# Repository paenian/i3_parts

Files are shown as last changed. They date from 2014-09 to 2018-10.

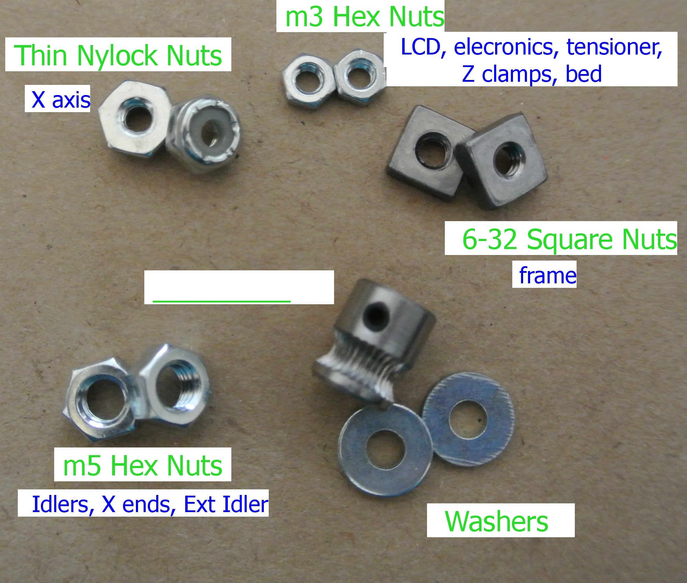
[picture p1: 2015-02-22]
bg6_pics/3D_PrinterBuild_6_Photos/labeled_parts/DSC_6048_Parts_NutsWashersAnd__.JPG

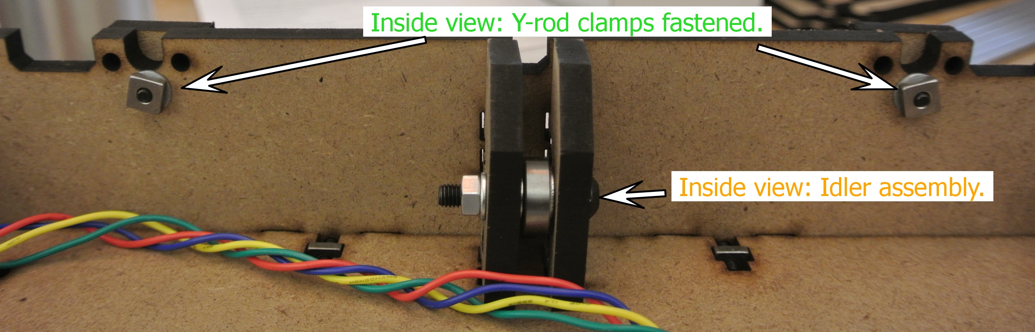
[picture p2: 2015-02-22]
bg6_pics/3D_PrinterBuild_6_Photos/DSC_6006-Y-rodClamps_InsideView_Annotated.JPG

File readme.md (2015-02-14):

A collection of parts that I use for my Graber i3 printers.  Original lasercut by Shane Graber is here: https://github.com/sgraber/Graber, and the source from Josef Prusa is here: https://github.com/josefprusa/Prusa3
<br><br>
Now featuring dual-strusion, including some parts I am using to convert my old Prusa v2 into a dual-extruder bowden machine.
<br><br>
<h4>Bill of Materails uploaded!</h4>
The full BOM is up: <pre>Paul's Prusa i3 kit - BOM.pdf</pre>
It includes everything I could think of.
<br><br>
Build Manual: <a href="https://github.com/paenian/i3_parts/wiki">https://github.com/paenian/i3_parts/wiki</a>
<br><br>
<h5>Tools</h5>
<ul>
<li>Metric Ball-end hex keys</li>
<li>Crescent Wrench</li>
<li>Soldering iron</li>
<li>Knife/scissors/wire strippers</li>
<li>Small Flathead screwdriver</li>
<li>Tweezers - preferably offset</li>
<li>Phillips screwdriver</li>
<li>Flush cutters (recommended)</li>
<li>Multimeter (recommended)</li>
</ul>
<br><br>
<h5>Major changes</h5>
<ul>
<li>Moved the LCD for better cable management</li>
<li>Added full-length top brace for increased rigidity</li>
<li>Added power-supply mounting holes</li>
<li>Added mounting holes for Rumba electronics</li>
<li>Modified bed to acommodate Y endstop rod mount</li>
</ul>

<br>
<h5>Lasercut Settings</h5>
<pre>
color - - - speed - - - power - - - corner power
Red - - - - 100 - - - -30 - - - - - 25
Green - - - 25 - - - - 30 - - - - - 25
Black - - - 12 - - - - 75 - - - - - 50
Blue - - - -12 - - - - 75 - - - - - 50
Magenta - - 12 - - - - 75 - - - - - 50
Teal - - - -12 - - - - 75 - - - - - 50
Yellow - - -12 - - - - 75 - - - - - 50
</pre>
<br>
Paul

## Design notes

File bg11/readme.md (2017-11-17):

Instructions for the BG11 build!

Firmware is copied from BG10 - will be updated later.  Nothing changing, just getting and testing the latest version of Marlin.

https://docs.google.com/presentation/d/1fhejMTiTbkoYrdEgeP_gHyqBJfEgC6iy6alJ2PzHSnQ/edit?usp=sharing

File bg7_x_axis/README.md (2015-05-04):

# This is Prusa iteration 3
Published under GPL v3
Developed primarily by Josef Prusa.

This is a new X-axis for the Build Group printers - primarily designed to eliminate parts, and make the build easier.

Also will include Y axis parts, namely a belt mount and a belt tensioner.

Paul

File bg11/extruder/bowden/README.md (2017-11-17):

The plan for Bowden is to simply re-use the extruder by adding a Bowden groovemount converter: https://www.filastruder.com/collections/e3d-spare-parts-and-accessories/products/bowden-couplings-all-types

So all you need is the clamp for mounting the hotend.

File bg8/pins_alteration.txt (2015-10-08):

Copy the pins_arduino.h file into this directory:
/home/paenian/reprap/arduino-1.6.5/hardware/arduino/avr/variants/mega

Better yet, we should copy the mega directory and create a new board variant - maybe look up how to do that?

Paul

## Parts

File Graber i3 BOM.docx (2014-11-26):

you will need additional parts to finish:

PART | QTT | | PART | QTT
6-32 x 3/4" | 41 | | Threaded rod
6-32 x 0.5" | 6 | | 5/16" x 2" (x & y-belt idler) | 2
6-32 x 1' | 2
6-32 x 1,1/4" (X-Car) | | | 5mm x 11.5" (Z-Axis) Alt - 10-24 x 11.5" | 2
6-32 x 1,3/4" | 4
Nut 6-32 Nylon Insert | 8
Nut 5/16" | 61 | | Smooth Rod
Nut M5 (.8mm / thread) Alt - 10-24 (.945mm / thread) | 2 | | http://www.use-enco.com/CGI/INSRIT?PMAKA=505-0240&PMPXNO=942271&PARTPG=INLMK32
Washers 6-32 | 2 | | 8mm x 13.5" (Y-Axis) | 2
Washers 5/16" | 6 | | 8mm x 12.5" (Z-Axis) | 2
M3 x 10mm (for step motors) | 2 | | 8mm x 15 3/4" (X-Axis) | 2
M3 x 25mm (RAMPS mount) | 15
M3 x 20-25 mm (Heated Bed) | 3 | -4 | Nema 17 Step motor | 5
M3 Nut Nylon Insert | 3-4 | | Micro Switch (end stops) | 3
Spring (heated bed mount) | 3-4 | | Electronics Board (RAMPS or other) | 1
Zip Tie 4" | 7
| | | Extruder (w/ 3 more 608zz bearings) | 1
608zz (for Y and X idler)
PVC Tubing 20mm (Z-Axis) | 2 | | LM8UU | 10
| 2

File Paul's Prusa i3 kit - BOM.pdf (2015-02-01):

Part | Size | Length/type | Quantity | description | Source | parts*bots | single part cost | total
Screws | 6-32 | 1/2" | 7 | Y motor mount, 3 hotend mount, 2 power supply mount | mcmaster | 7 | $0.12 | $0.85
| | 3/4" | 50 | frame | mcmaster | 50 | $0.20 | $9.80
| | 1 1/4" | 7 | 6 X carriage, 1 extruder clamp | mcmaster | 7 | $0.30 | $2.11
| | 1 3/4" | 8 | X ends | mcmaster | 8 | $0.62 | $4.95
| m3 | 10mm | 30 | 4 X, 3 Y, 8 ZZ, 3 E, 8 z clamp, 4 endstops | mcmaster | 30 | $0.07 | $2.06
| m3 | 20mm | 15 | 4 LCD, 4 electronics, 4 heatbed mount, 1 extruder tensioner, 2 endstops | mcmaster | 15 | $0.09 | $1.28
| m4 | 18mm | 3 | Power supply mount | mcmaster | 3 | $0.11 | $0.33
| m5 | 30mm | 6 | 2 X and Y Idler, 4 spool rollers | mcmaster | 6 | $0.12 | $0.74
| m5 | 14mm | 1 | extruder idler | mcmaster | 1 | $0.12 | $0.12
| All screws are button-head except the m4
Nuts | 6-32 | square | 58 | | mcmaster | 58 | $0.02 | $0.95
| 6-32 | thin nylock | 14 | | mcmaster | 14 | $0.03 | $0.37
| m5 | hex | 9 | 2 for x ends, 2 for idler screws, 1 extruder idler, 4 spool rollers | mcmaster | 9 | $0.02 | $0.19
| m3 | hex | 27 | 4 LCD, 4 electronics, 4 heatbed, 1 idler, 8 z clamp, 6 endstop | mcmaster | 27 | $0.01 | $0.38
Washers | 6-32 | flat | 100 | frame, motors, ps, etc. This washer will fit m3, m4 and 6-32 screws just fine. | mcmaster | 100 | $0.01 | $1.35
| m5 | flat | 6 | idlers | mcmaster | 6 | $0.02 | $0.13
Bearings | lm8uu | linear | 10 | 3 X, 3 Y, 4 Z | aliexpress | 10 | $0.60 | $6.00
| 605zz | roller | 7 | 3 idlers, 4 spool rollers | aliexpress | 7 | $0.42 | $2.94
Smooth Rod | m8 | 400mm | 2 | X rods - 15.75" | misumi | 2 | $8.44 | $16.88
| | 342mm | 2 | Y rods - 13.5" | misumi | 2 | $8.44 | $16.88
| | 318mm | 2 | Z rods - 12.5" | misumi | 2 | $8.44 | $16.88
| m8 | 36" drill rod | 3 | | mcmaster | 3 | $5.70 | $17.10
Threaded Rod | m5 | 300mm | 2 | mcmaster | 2 | $5.12 | $10.24
Wire | 16 gauge power wire | 2 conductor | 5 | 2 2' runs PS to electronics | mcmaster powe | 5 | $0.69 | $3.45
| | | | 1 1' run electronics to heatbed | | 1 | $0.69 | $0.69
| | | | cut up a bit to install power switch | | 0 | $0.69 | $0.00
Other | motors | nema 17 | 5 | | kysan | 5 | $16.00 | $80.00
| electronics | rumba | 1 | Includes heatbed, pulleys, belts, LCD, grub screws, wiring | reprapdiscount | 1 | $159.00 | $159.00
| Power Switch | | 1 | | amazon | 1 | $6.00 | $6.00
| Power cord | computer cord | 1 | | amazon | 1 | $5.00 | $5.00
| fuse | | 1 | | amazon | 1 | $1.20 | $1.20
| female spade connectors | 22/18 | 6 | | http://www.ama (http://www.amazon.com/gp/product/B001766LZO/ref=ox_sc_act_title_1?ie=UTF8&psc=1&smid=A1PH6OFMJYJKNX) | 6 | $0.13 | $0.80
| power supply | 24v 15a | 1 | | amazon | 1 | $25.00 | $25.00
| induction sensor | 8mm range, 18 | 1 | | amazon | 1 | $8.20 | $8.20
| plastic | for me to print w | 1 | | my print cave | 1 | $20.00 | $20.00
| borosilicate glass | 8x8.5x1/8 | 1 | | cincinatti gasket | 1 | $22.00 | $22.00
| Kapton tape sheet | 8x8 | 2 | | amazon | 2 | $3.59 | $7.18
| plastic reel | for you | 1 | | Microcenter | 1 | $25.00 | $25.00
| MDF sheet | 1/4"x48x24 | 1 | Cut to 39x24 before laser cutting | home depot | 1 | $6.00 | $6.00
| Laser Cutting | in hours | 1.5 | it's a lot of cuts. | Nova Labs | 1.5 | $20.00 | $30.00
| Paul putting all this toget | brownie points | 16 | | | 16 | | $0.00
| Stanley organizer | 25 compartment | 1 | | http://www.ama (http://www.amazon.com/Stanley-25-Removable-Compartment-Professional-Organizer/dp/B00005QWYF) | 1 | $13.00 | $13.00
| hotend | e3d V6 | 1 | | filastruder | 1 | $80.00 | $80.00
| Bed Clips | 3/4" wide, 5/16" | 4 | | mcmaster | 4 | $0.07 | $0.28
| Zip Ties | 4" | 25 | | mcmaster | 25 | $0.02 | $0.55
Printed Parts | Power Supply Cover | 1 | 1 | 0
| Z clamps | 4 | 4 | 0
| Endstops | 2 | 2 | 0
| Stop Switch | 1 | 1 | 0
| Encoder Dial | 1 | 1 | 0
| Extruder Mount | 1 | 1 | 0
| Extruder Mount | 1 | 1 | 0
| Induction Mount | 1 | 1 | 0
Budget | | | $550
Totals | | pre-cut hardened steel | $588.77
| | drill rod, needs to be cut to length | $555.23
# of Printers | 1 | pre-cut leftover | -$39

| | drill rod leftover | -$5
| | Note: Shipping isn't included anywhere.

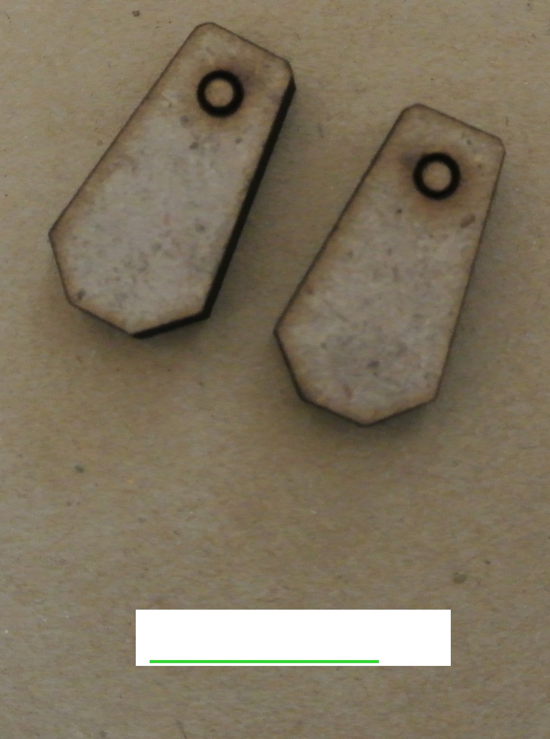
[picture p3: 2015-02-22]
bg6_pics/3D_PrinterBuild_6_Photos/labeled_parts/DSC_6039_Cropped.JPG

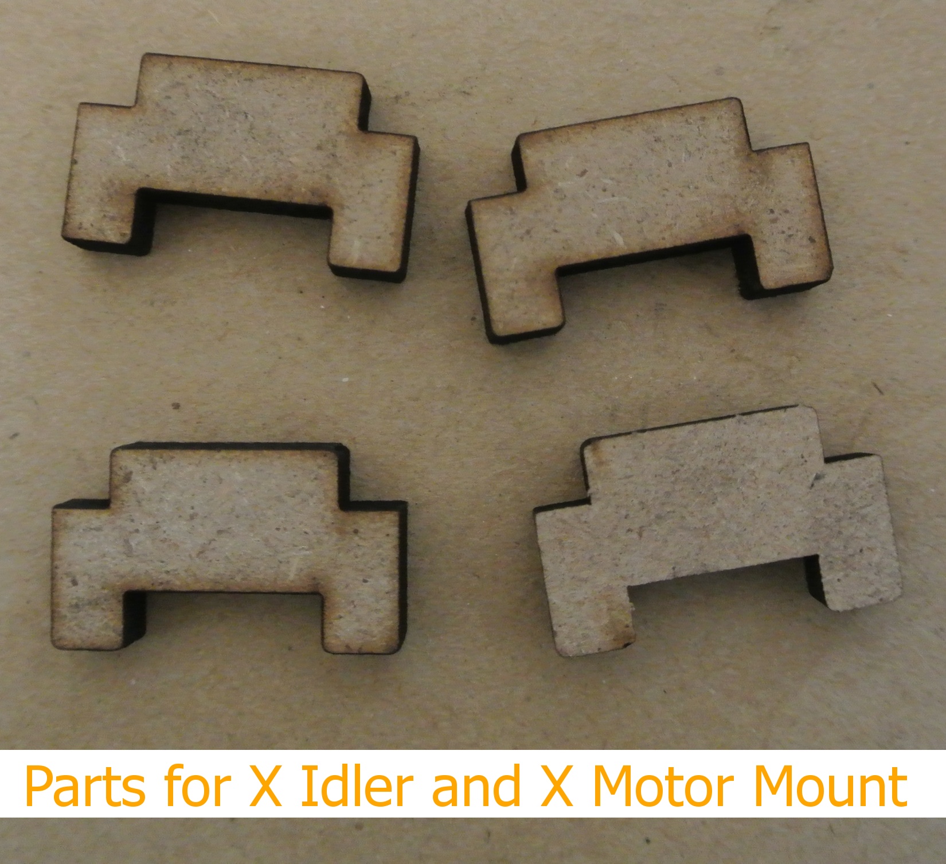
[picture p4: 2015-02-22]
bg6_pics/3D_PrinterBuild_6_Photos/labeled_parts/DSC_6040_Parts_X-IdlerAndX-MotorMount.JPG

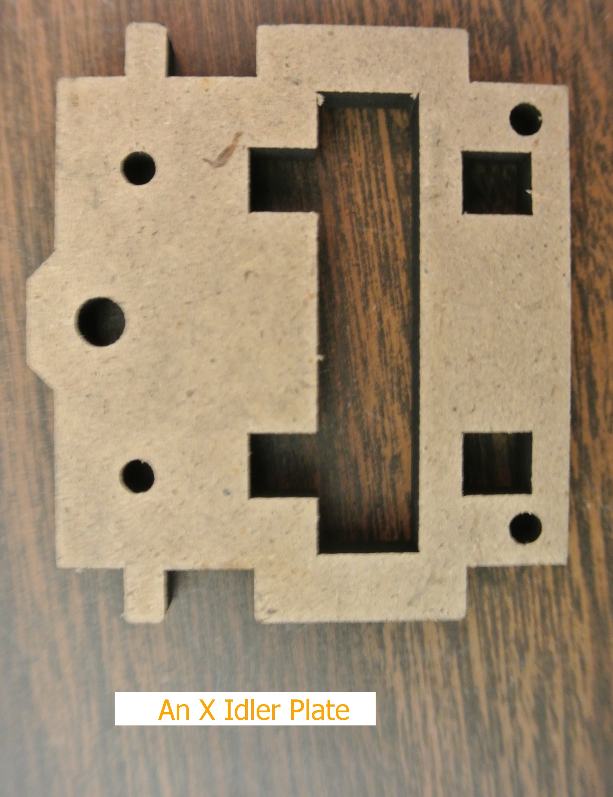
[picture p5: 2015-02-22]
bg6_pics/3D_PrinterBuild_6_Photos/labeled_parts/DSC_6013_Parts_X-IdlerPlate1.JPG

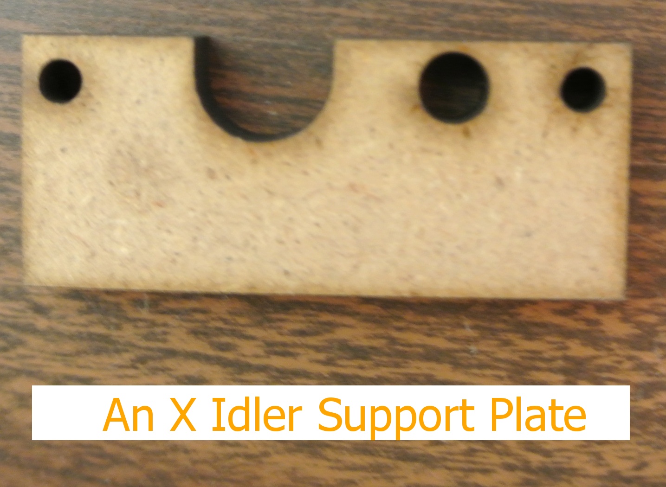
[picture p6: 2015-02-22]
bg6_pics/3D_PrinterBuild_6_Photos/labeled_parts/DSC_6021_Parts_X-IdlerSupportPlate2.JPG

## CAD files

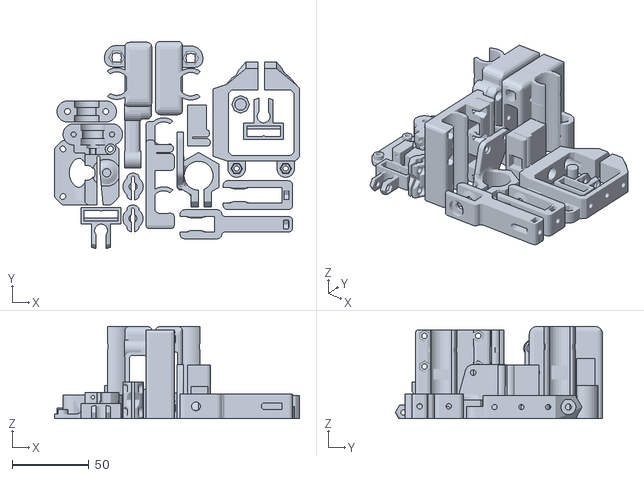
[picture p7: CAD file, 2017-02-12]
bg10/full_plate.stl
159.9 x 135.4 x 60.2

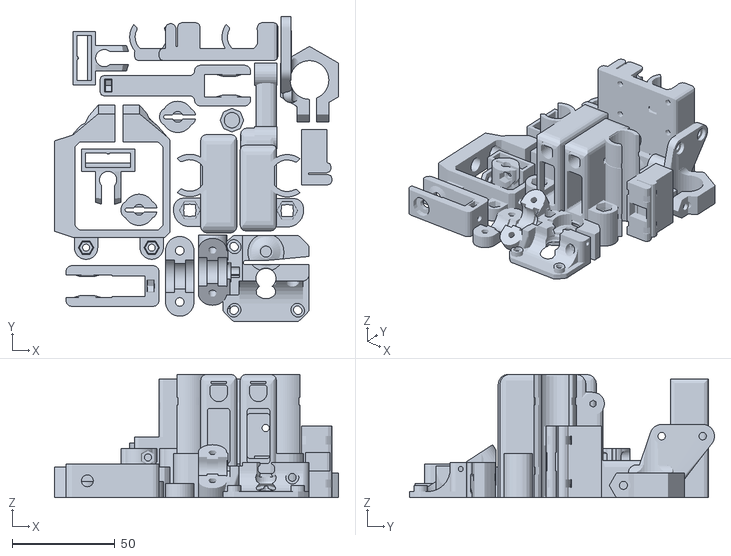
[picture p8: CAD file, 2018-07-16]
bg11/full_plate.stl
138.6 x 148.7 x 60.2

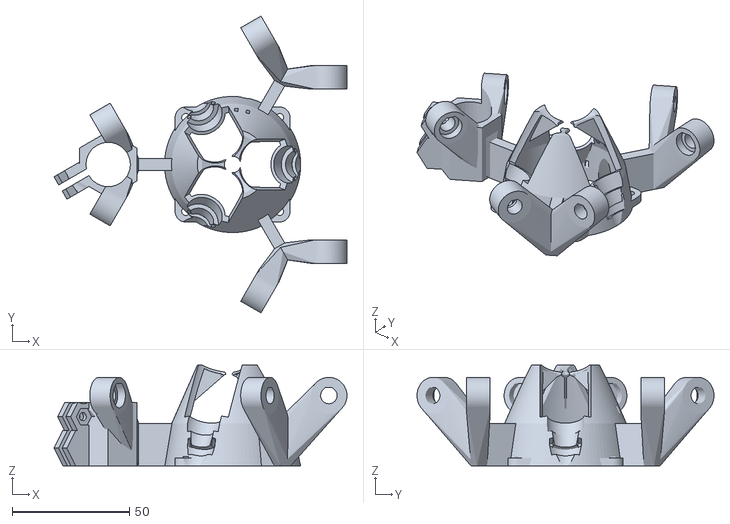
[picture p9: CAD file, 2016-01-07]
bg8/x_axis/diamond_hotend_assembly.stl
124.8 x 126.5 x 43.0

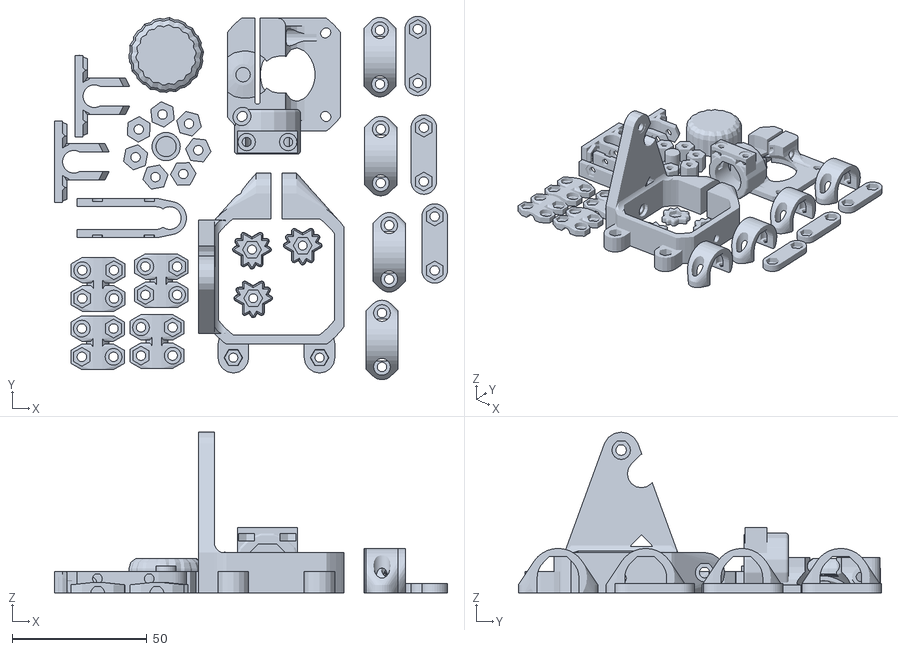
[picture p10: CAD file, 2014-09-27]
i3_full_plate.stl
145.8 x 134.8 x 59.7

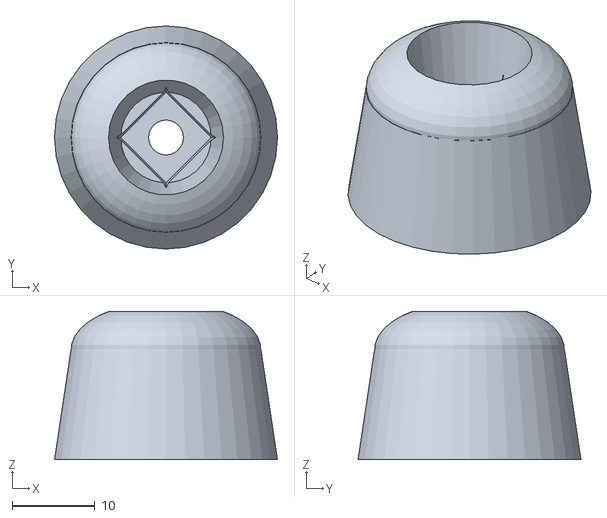
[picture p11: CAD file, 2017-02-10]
bg10/extras/foot.stl
26.9 x 26.9 x 17.9

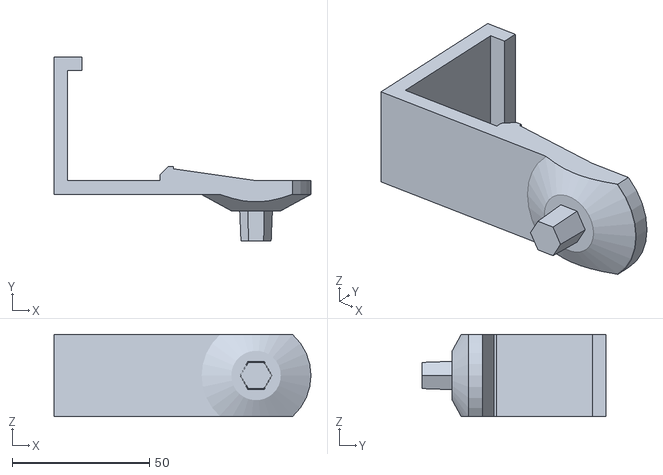
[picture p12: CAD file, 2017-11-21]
bg10/extras/spool_roller/spool_bearing_mount.stl
93.5 x 67.0 x 30.0

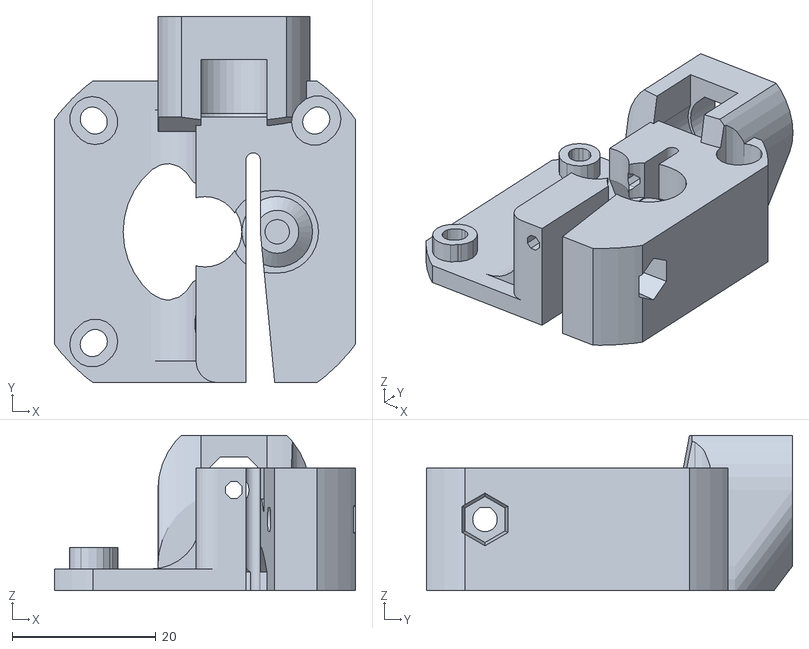
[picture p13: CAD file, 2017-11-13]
bg10/extruder/bowden/motormount_extruder_bowden.stl
42.0 x 51.0 x 21.6

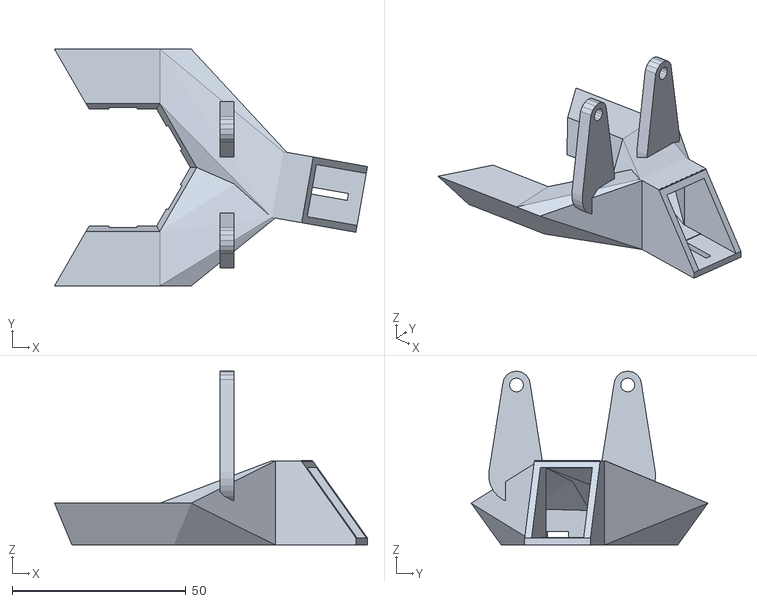
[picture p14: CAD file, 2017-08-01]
bg10/extruder/cooling_fan_mount.stl
90.0 x 68.1 x 50.0

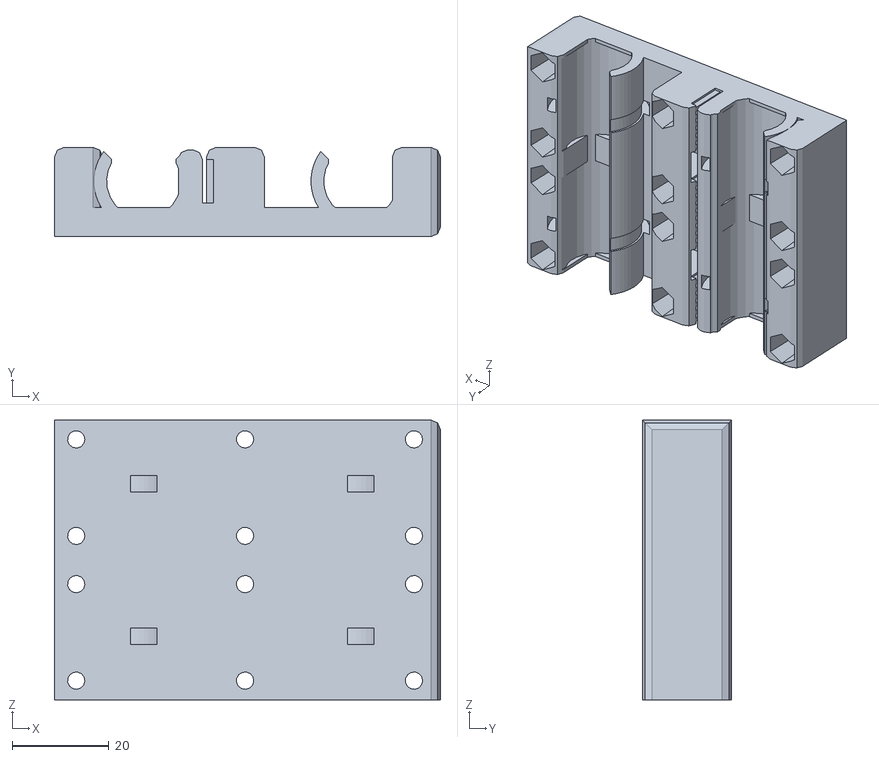
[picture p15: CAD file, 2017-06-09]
bg10/x_axis/x-carriage_aero.stl
80.0 x 18.5 x 58.0

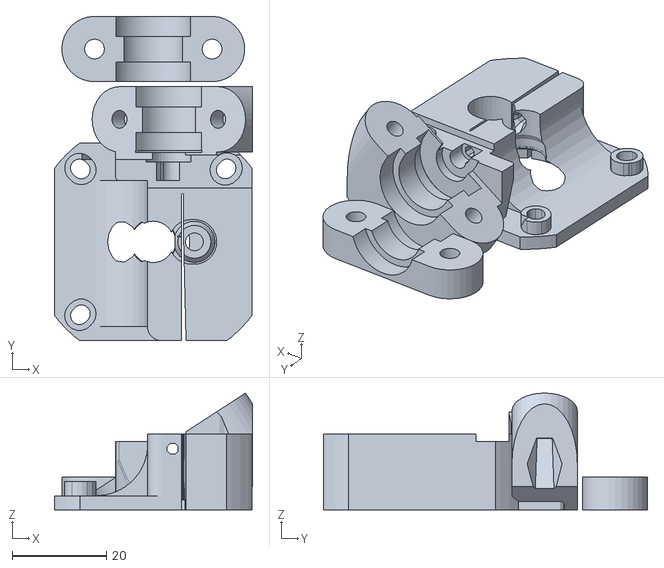
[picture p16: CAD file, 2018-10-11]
bg11/extras/bondtech/motormount_bondtech.stl
42.1 x 69.0 x 24.9

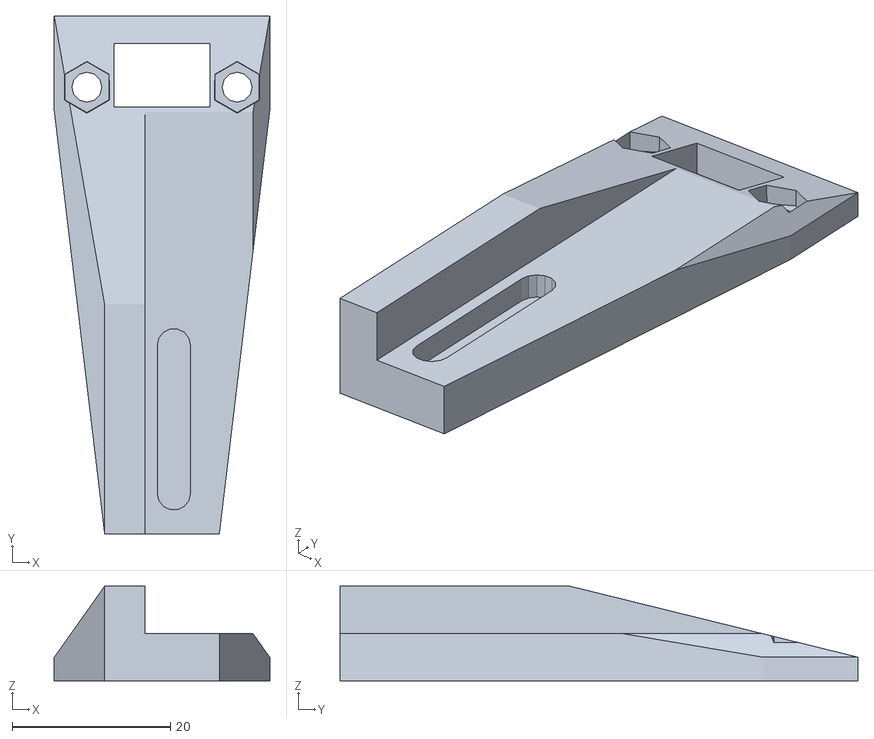
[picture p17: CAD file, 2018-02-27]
bg11/extras/diff_ir_drop_mount.stl
27.2 x 65.5 x 12.0

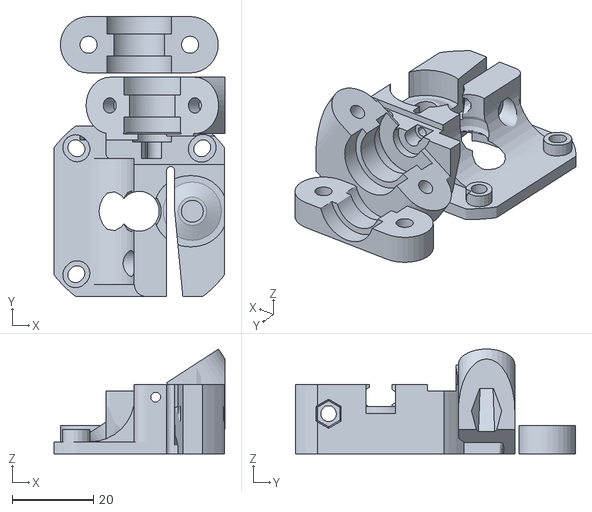
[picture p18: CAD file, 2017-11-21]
bg11/extruder/motormount_extruder_v2.stl
42.1 x 69.0 x 25.9

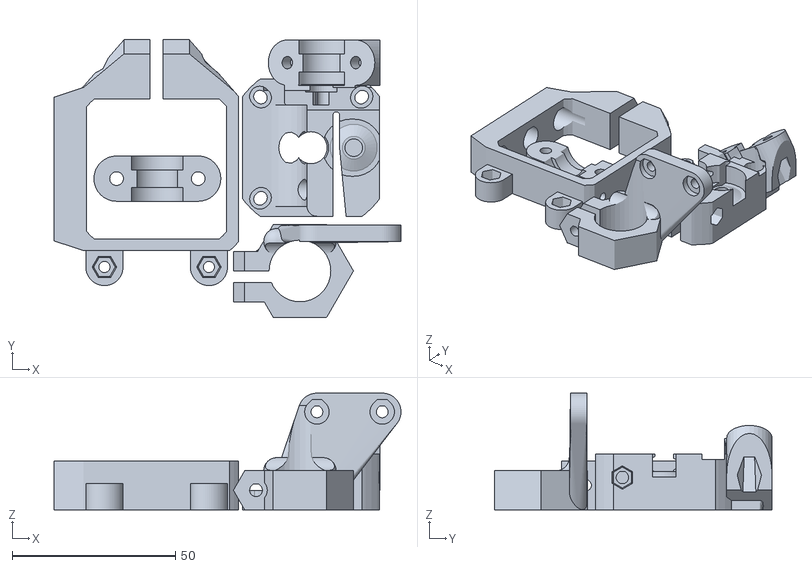
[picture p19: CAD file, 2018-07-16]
bg11/extruder_plate.stl
106.3 x 85.0 x 35.8

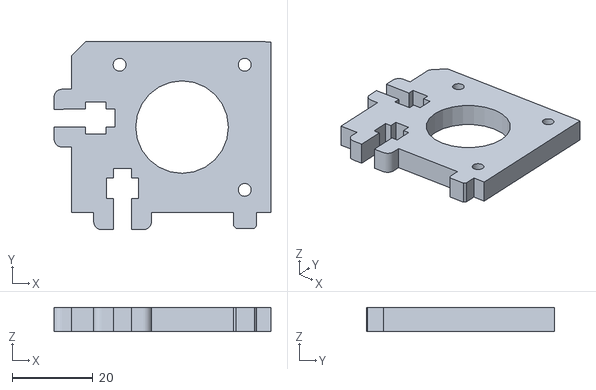
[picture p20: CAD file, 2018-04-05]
bg11/frame/y_motor_mount.stl
53.8 x 46.7 x 6.00

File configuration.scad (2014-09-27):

////////////////////////////
//  This is a Delta printer design by Paul Chase.
////////////////////////////


slop = .2;
wall = 5;



////////////////////////////
//Standard Sizes
////////////////////////////
m3_nut_rad = 6.05/2+slop;
m3_nut_height = 2.4+slop;
m3_rad = 3/2+slop;
m3_cap_rad = 3.25;
m3_washer_rad = 7/2+slop;

m4_nut_rad = 7.66/2+slop;
m4_nut_height = 3.2;
m4_rad = 4/2+slop;
m4_cap_rad = 7/2+slop;
m4_washer_rad = 2*m4_rad;

m5_nut_rad = 9.05/2+slop;
m5_nut_height = 4.7;
m5_rad = 5/2+slop;
m5_cap_rad = 8/2+slop;
m5_washer_rad = 2.1*m5_rad;
m5_cap_height = 2;

//for the tiny m3 bearings
623_width = 4;
623_rad = 10.05/2+slop;
623_bore = m3_rad;
623_inner_shoulder = 623_bore+(623_rad-m3_rad)/3;
623_outer_shoulder = 623_rad-(623_rad-m3_rad)/3;

//spacers
spacer_rad = 6/2+slop;
spacer_len = 2-slop/2;

eccentric_rad = 7.2/2+slop;
eccentric_washer_rad = 15/2+slop;
eccentric_screw_rad = 7/2+slop;
eccentric_height = 2.5;



//////////////////////////////
//Useful global functions
//////////////////////////////
module cap_cylinder(r=1, h=1, center=false){
	render() union() {
		cylinder(r=r, h=h, center=center);
		intersection(){
			rotate([0,0,22.5]) cylinder(r=r/cos(180/8), h=h, $fn=8, center=center);
			translate([0,-r/cos(180/4),0]) rotate([0,0,0]) cylinder(r=r/cos(180/4), h=h, $fn=4, center=center);
		}
	}
}

module 623_bearing(){
	union(){
		//outer
		color([.75,.75,.75]) difference(){
			cylinder(r=623_rad, h=623_width);
			translate([0,0,-.1]) cylinder(r=623_outer_shoulder, h=623_width+.2);
		}
		//middle
		color([.25,.25,.25]) difference(){
			translate([0,0,.25]) cylinder(r=623_outer_shoulder, h=623_width-.5);
			translate([0,0,-.1]) cylinder(r=623_inner_shoulder, h=623_width+.2);
		}
		//inner
		color([.75,.75,.75]) difference(){
			cylinder(r=623_inner_shoulder, h=623_width);
			translate([0,0,-.1]) cylinder(r=623_bore, h=623_width+.2);
		}
	}
}

module 623_bearing_cone(rad = 623_rad, height = 5, solid=1, nut_trap=0){
	cone_h = rad-623_inner_shoulder;
	if(nut_trap==1){
		if(solid==1){
			union(){
				echo("cone_height", cone_h);
				cylinder(r1=623_inner_shoulder, r2=rad, h=cone_h);
				translate([0,0,cone_h]) cylinder(r=rad, h=height-cone_h);
			}
		}else{
			//bore
			translate([0,0,-.1]) rotate([0,0,90]) cap_cylinder(r=623_bore, h=height+.5);
			//nut trap
			#translate([0,0,height-m3_nut_height]) hull(){
				cylinder(r1=m3_nut_rad, r2=m3_nut_rad+.5, h=m3_nut_height+.5, $fn=6);
				translate([30,0,0]) cylinder(r1=m3_nut_rad, r2=m3_nut_rad+.5, h=m3_nut_height+.5, $fn=6);
			}
		}
	}else{
		if(solid==1){
			cylinder(r1=623_inner_shoulder, r2=rad, h=height);
		}else{
			translate([0,0,-.1]) rotate([0,0,90]) cap_cylinder(r=623_bore, h=height+.5);
		}
	}
}

module 623_bearing_mount(rad = 623_rad+2, height=5, solid=1){
	if(solid==1){
		union(){
			cylinder(r=rad, h=height);
		}
	}else{
		translate([0,0,height-623_width+slop]) cap_cylinder(r=623_rad, h=623_width*2);
		//translate([0,0,height-623_width]) cap_cylinder(r=623_outer_shoulder, h=623_width*2);
		translate([0,0,-height]) cap_cylinder(r=m3_cap_rad+.25, h=height*3);
	}
}

module barbell (x1,x2,r1,r2,r3,r4)
{
	x3=triangulate (x1,x2,r1+r3,r2+r3);
	x4=triangulate (x2,x1,r2+r4,r1+r4);
	render()
		difference(){
			union(){
				translate(x1) circle (r=r1);
				translate(x2) circle(r=r2);
				polygon (points=[x1,x3,x2,x4]);
			}
		translate(x3) circle(r=r3,$fa=5);
		translate(x4) circle(r=r4,$fa=5);
	}
}

function triangulate (point1, point2, length1, length2) =
point1 + length1*rotated(
atan2(point2[1]-point1[1],point2[0]-point1[0])+
angle(distance(point1,point2),length1,length2));

function distance(point1,point2)=
sqrt((point1[0]-point2[0])*(point1[0]-point2[0])+
(point1[1]-point2[1])*(point1[1]-point2[1]));

function angle(a,b,c) = acos((a*a+b*b-c*c)/(2*a*b));

function rotated(a)=[cos(a),sin(a),0];
function rotate_vec(v,a)=[cos(a)*v[0]-sin(a)*v[1],sin(a)*v[0]+cos(a)*v[1]];

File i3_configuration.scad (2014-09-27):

////////////standard variables.  Shouldn't need to change 'em.  Except maybe slop.
motor_w = 42;
motor_r = 50/2;

m3_nut_rad = 6/cos(30)/2;
m3_nut_height = 3;
m3_rad = 1.8;
m3_cap_rad = 3.25;

m4_rad = 2+slop;
m4_nut_rad = 7.8/2+slop;
m4_nut_height = 3.2;
m4_cap_rad = 7/2+slop;

m5_nut_rad = 8.4/cos(30)/2+slop;
m5_nut_height = 4+slop;
m5_rad = 2.8;

//english sizes - 6-32 - for graber i3 clamp
632_dia = 3.5;
632_rad = 632_dia/2+slop;
632_nut_rad = 8.25/cos(45)/2;
632_cap_dia = 6.5;
632_cap_rad = 632_cap_dia/2+slop;
632_cap_height = 2+slop;
632_nut_height = 5;

$fn=32;

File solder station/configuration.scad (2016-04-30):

mdf_wall = 6.5;
mdf_tab = 15;

wall = 5;

screw_slop = .2;
slop = .2;
laser_slop = -.1;

smooth_rod_rad = 10/2+laser_slop+.1;

//these can't change - measured values.
beam = 20;
bed_screw_sep = 309;
bed = 300;

layer_height=.2;

//this is for using the big idlers
//idler_rad = 17.5/2;
//idler_flange_rad = 22/2;

//this is using flanged bearings, and no plastic
idler_rad = 10/2;
idler_flange_rad = 15/2;

pulley_rad = 13/2;
pulley_flange_rad = 18/2;

//using the mini V-wheels
wheel_rad = 11.5/2;
wheel_clearance = 18;
wheel_height = 9;
wheel_flange_rad = 16/2;

eccentric_rad = 7.3/2;
eccentric_flange_rad = 11/2;

//frame lengths - may be dependent on wall above.
frame_x = 500;  //we lose more in X because of the endcaps - it's where all the motors etc. will hide.
frame_y = 420;  //(420-300)/2-beam=40mm clearance on either side of the printer.
frame_z = 420;  //because square is nice.

foot_height = 60;       //tall foot, cuz the Z motor will be underneath.

echo("BOM: 4, reg rail, 2020", frame_x, "Frame");

//motor size and placement variables
motor_w = 42;
motor_r = 52/2;
motor_y = frame_y/2-beam-pulley_rad; //distance motors are from the center.

belt_thick = 6;
belt_width = 2;


//gantry - might want to make it bigger
echo("BOM: 1, v-rail, 2020", frame_y, "Gantry");

//bed lengths
bed_x = 300+beam*2;
bed_y = 300;  //the screwholes on the bed should line up with the long_bed rails.
echo("BOM: 2, reg rail, 2020", bed_x, "Bed mount");
echo("BOM: 3, reg rail, 2020", bed_y, "Bed mount");  //might want more than three - to hold insulation well.

//standard screw variables
m3_nut_rad = 6.01/2+slop;
m3_nut_height = 2.4;
m3_rad = 3/2+slop;
m3_cap_rad = 3.25;
m3_cap_height = 2;

m4_nut_rad = 7.66/2+slop;
m4_nut_height = 3.2;
m4_rad = 4/2+slop;
m4_cap_rad = 7/2+slop;
m4_cap_height = 2.5;

m5_nut_rad = 8.79/2;
m5_nut_rad_laser = 8.79/2-.445;
m5_nut_height = 4.7;
m5_rad = 5/2;
m5_cap_rad = 10/2+slop;
m5_cap_height = 3;


//some enums
MALE = 1;
FEMALE = -1;

//makes all the holes have lots of segments
$fs=.5;
$fa=.1;

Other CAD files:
bg9/full_plate.stl
bg11/small_bits/z_clamp.stl
bg11/x_axis/inc/splitter_coupler.stl
bg7_x_axis/anglefan.stl
bg11/x_axis/configuration.scad
1.75_bowden_tap_m5idler.stl
1.75_grooveclamp_clamp.stl
1.75_grooveclamp_m5idler.stl
1.75_groovemount_m5idler.stl
1.75_mark8_bowden_m5idler.stl
1.75_mark8_grooveclamp_m5idler.stl
End_Stop_Holder.scad
LM8UU_holder_ziptie.scad
PowerSupply.scad
PowerSupply.stl
anglefan.stl
bg10/extras/spool_roller/bearing.scad
bg10/extras/spool_roller/bearing_lifter.scad
bg10/extras/spool_roller/spool_bearing.scad
bg10/extras/spool_roller/spool_roller.scad
bg10/extras/spool_roller/spool_roller.stl
bg10/extras/spool_roller/top_spool_roller.stl
bg10/extruder/aero_flange.stl
bg10/extruder/cooling_fan_mount_rakish.stl
bg10/extruder/extruder_mount.stl
bg10/extruder/extruder_mount_aero.stl
bg10/extruder/motormount_extruder_v2.scad
bg10/extruder/motormount_extruder_v2.stl
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

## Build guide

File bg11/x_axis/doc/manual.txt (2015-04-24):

Assembly

This document will guide you through putting together your Prusa i3.
Please read it through briefly before starting your build, and make sure you have everything you need to continue.
It's frustrating to be stuck with a half-finished machine because you are missing a part or tool.
It's recommended to do the assembly with 2 or more people. If you are doing this alone, do the instructions in order.
If there are two of you, each step is marked P1 or P2. Decide which one of you is Player 1 and act accordingly.
If there are more than two of you, split into two teams.

===Assemble the extruder (P1)===
There are multiple forms of extruder. These instructions cover two common variants.

==The gregstruder==
Plastic parts needed:
-Extruder body
-Extruder idler
-Extruder large gear
-Extruder small gear
Other parts needed:
-1 NEMA17 motor
-1 hotend
-1 M3x8 grub screw
-6 M3 nuts
-3 M3x40 bolts
-1 M8x20 grub screw
-1 M8 hobbed bolt
-4 M8 washers
-2 M8 nuts
-3 608 skateboard bearings
-3 M3x10 bolts
(optional) 2 short, stiff springs or silicone pads
Tools needed
-Wrench/spanner to fit M8 (preferably 2)
-Soldering iron
-Drill with 8mm and 3mm bits
-File
-Screwdriver or allen key to fit your M3 bolt heads and the M3 grub screw

Take the extruder body and snap off the small support piece attached to it. It should separate easily. If it leaves a messy surface, clean the surface up.
Use the drill to drill through the 8mm hole in the extruder body, the 3mm holes for the motor bolts, the 2 3mm mounting holes on the bottom and the 3mm hole for the idler (where the support piece was).
Melt two M3 nuts into the nut traps over the mounting holes.
Drill through the filament channel to make sure it's clear.
Place 1 608 bearing on the M8x20 grub screw and push it into the idler. It will only fit if the bearing is on the middle of the grub screw. It will click in place.
Attach the idler to the extruder body and fix it with the M3x40 bolt. Make sure the bolt head is on the FLAT side of the extruder body. You can put a nut on the bolt if you want, but don't tighten it very tightly.
Place an M3 nut in the small gear and fix it in place with the M3x8 grub screw. Slide the gear onto the motor shaft and fix it in place with the grub screw. Do not overtighten, and make sure the motor can turn freely with the gear in place.
Attach the motor to the extruder body with the 3 M3x10 bolts. The bolt heads go on the FLAT side of the extruder body.
Place 2 608 bearings in the recesses in the extruder body. 
Place the hobbed bolt in the large gear. If it's too loose, pad it a bit until it sits tight. Place two washers on the opposite (flat) side of the gear and slide the hobbed bolt through the two bearings into the extruder body. The gear teeth will mesh with the small gear already there. If they don't, adjust the position of the motor and/or the gear on the motor shaft until they do. Make sure the bobbing on the bolt aligns with the filament channel. If necessary, add another washer between the gear and the extruder body. Place a washer followed by 2 M8 nuts on the opposite side of the extruder body to fix the bolt in place.
If you are using springs or silicone pads, place those on the remaining two M3x40 bolts. Place two nuts into the nut recesses above the two bearings. Use the M3x40 bolts to fix the idler in place. You will adjust the tension later when you insert filament, so don't worry about that for now. 
Assemble your hotend according to your specific hotend's assembly instructions. I am assuming you have a hotend that is matched to your extruder body.
Attach the hotend to the extruder. If your hotend has a flat mounting plate, make sure the holes on it align with the holes on the extruder body so that the filament channel leads into the hotend. Redrill holes as necessary if something does not fit.

==The raldrich geared stepper extruder==

Plastic parts needed:
-Extruder body
-Extruder idler
-Extruder body spacer
Other parts needed:
-1 geared stepper motor
-1 hotend
-2 M3x30 bolt
-6 M3 nuts
-1 filament drive gear
-1 M3x8 grub screw
-1 M4 x20 bolt
-1 624 bearing
-4 M3x40 bolts
-4 M3 washers
(optional) 4 short, stiff springs or silicone pads
Tools needed
-Soldering iron
-Drill with 8mm and 3mm bits
-File
-Screwdriver or allen key to fit your M3 and M4 bolt heads and the M3 grub screw

Use the drill to drill through the 3mm holes for the motor bolts, the 2 3mm mounting holes on the bottom and the 4mm hole in the idler.
Drill through the filament channel to make sure it's clear.
Place the 624 bearing in the idler and fix it with the M4x20 bolt.
Place the spacer on the motor and make sure it aligns correctly with the extruder body.
Attach the drive gear to the motor shaft with the grub screw. Adjust the position of the drive gear to align with the filament channel.
Use the M3x30 bolts and the M3 nuts to fix the extruder body to the motor, sandwiching the spacer plate between them.
Place washers on the M3x40 bolts.
If you are using springs or silicone pads, place those on the remaining M3x40 bolts.
Place M3 nuts into the nut traps of the extruder body.
Attach the idler to the extruder body, so that the bearing presses against the drive gear.
Assemble your hotend according to your specific hotend's assembly instructions. I am assuming you have a hotend that is matched to your extruder body.
Attach the hotend to the extruder. If your hotend has a flat mounting plate, make sure the holes on it align with the holes on the extruder body so that the filament channel leads into the hotend. Redrill holes as necessary if something does not fit.

===Assemble the X axis (P2)===
Plastic parts needed:
-x axis motor end
-x axis idler end
-x carriage
Other parts needed:
-1 NEMA17 stepper motor
-1 T2.5 belt
-3 M3x10 bolt
-1 belt drive pulley
-1 M3x8 grub screw
-1 ??? bolt
-1 ??? bearing
-7 linear bearings
-7 M3x25 bolt with nut and washers
-2 smooth rods
Tools needed
-Screwdriver or allen key to fit your M3 bolt heads and the M3 grub screw

The X axis consists of 3 parts - the motor end, the idler end, and the carriage. 
Insert four linear bearings (two per part) into the motor and idler ends of the x axis, gently fix them in place with M3x25 screw
Slide a smooth rod through each pair of linear bearings to make sure they slide smoothly and don't move around. If they do move around, tighten the screw. Remove the smooth rods
Insert two smooth rods into the motor end of the X axis (the one with the three mounting points for the motor). Push them in as far as they will go.
Insert three linear bearings into the carriage. Slide the carriage onto the smooth rods and fix them with screws as with x ends.
Attach the idler bearing onto the idler end using an ??? bolt.
Push the idler onto the smooth rods, trapping the carriage in. Make sure the carriage can move along the rods with minimal effort.
Attach a NEMA17 motor to the motor end using 3 M3x10 bolts. The bolt heads will sink into the part, and the motor will be on the side opposite the linear bearings.
Place a pulley on the motor and fasten it to the shaft using a grub screw. Make sure the belt path is aligned with the gap in the x end pieces.
Insert a belt into the carriage belt holder such that it meshes with the printed teeth.
Thread the belt through the motor and idler ends, so that it runs over the bearing and the pulley. Insert the other end of the belt into the belt holder.
Do not cut the belt to size yet, as we will still have to adjust the location of the idler end along the smooth rods.

===Assemble the Y axis(P2)===
Plastic parts needed:
-y axis motor holder
-4 y corners
-y axis idler 
-y belt clamp
-3 y bearing holders
Other parts needed:
-1 23x23cm 12mm plate (9"x9" 1/2" thick for people in inchy countries) (may be thinner)
-1 heated bed PCB, with wires attached
-1 glass plate covered with Kapton or PET tape
-1 NEMA17 stepper motor
-1 T2.5 belt
-2 M3x10 bolt
-1 belt drive pulley
-1 M3x8 grub screw
-1 ??? bolt
-1 ??? bearing
-3 linear bearings
-3 M3x25 bolt with nut and washers
-2 405mm smooth rods
-22 M8 nuts (substitute 5/16" for M8 in inchland)
-22 M8 washers
-12 M10 nuts (?? in inchland)
-12 M10 washers
-4 140mm M8 (5/16") threaded rod (longer is ok)
-2 430mm M10 (??/16") threaded rod (longer is ok)
-9 3.5x12mm wood screws (or shorter if your plate is thinner)
Tools needed:
-Screwdriver to fit your wood screws
-Screwdriver or allen key to fit your M3 bolt heads and the M3 grub screw
-13mm wrench
-Another 13mm wrench (optional but violently recommended)
-17mm wrench
-Another 17mm wrench (optional, but...)
-Pencil or marker that is visible on the plate material
-Drill with 3.2mm (1/8") or 3mm drill bit
-Tape for holding things in place

Place the belt drive pulley on the motor shaft and tighten it with the grub screw.
Attach the motor to the y axis motor holder using two M3x10 bolts. (ystep1.png)
Thread two of the 140mm threaded rods through the motor holder. It should sit about 1/3 along the length of the rods, so that the motor is approximately centered.
Use 4 M8 washers and nuts to fix the motor holder in place on the rods. (ystep2.png)
Place a ??? bearing in the idler and fix it with the ??? bolt.
Attach the idler to one of the remaining 140mm rods. Fix it with a nut and washer on each side. (ystep3.png)
Place a pair of washers surrounded by nuts around the middle of each of the 430mm threaded rods.
Place a nut and a washer on one end of each of the 430mm threaded rods. (ystep4.png)
Snap a smooth rod into one of the y corners.
Thread one end of the 430mm threaded rod through the y corner piece so it goes parallel to the smooth rod with the nut and washer against the plastic part.
Put a washer and a nut on the outside of the plastic piece, fixing it to the threaded rod. (ystep5.png)
Put a nut followed by a washer onto the other end of the threaded rod.
Add another plastic y corner to the smooth and threaded rod's other end.
Put a washer and a nut on the outside of the plastic piece, fixing it to the threaded rod. 
Adjust the inner nut so the smooth rod is snugly held in place.(ystep6.png)
Repeat this procedure for the other 430mm threaded rod.(ystep7.png)
Place a nut and a washer on one end of each of the 140mm threaded rods. (ystep8.png)
Place the assembled smooth and threaded rods on the ends of the 140mm rods. Adjust the motor and idler position if necessary. (ystep9.png)
Place a nut and washer on the outside end of each of the 140mm rods. Do not tighten yet. (ystep10.png)
Place an object of 10cm width between the smooth rods. One of the frame panels might be useful for this.
Using the 10cm reference, make sure the distance between smooth rods is the same on both ends. 
Measure as close as you can to the motor, and as close as you can to the idler. 
Adjust the inner nuts and tighten the outer nuts, while checking the distance repeatedly. 
Use two wrenches to tighten the nuts without moving the plastic part along the rod.
Once done, pop the smooth rods out of the plastic parts. (ystep11.png)
Place the linear bearings in the linear bearing holders, fix them firmly with M3x25 screws
Slide them onto the rods. Two on one rod, one on the other.
Place your heated bed PCB on the plate and tape it down so it doesn't move around.
Mark and drill the 4 corner holes of the PCB with a 3.2mm (1/8") or 3mm drill.
Remove the heated bed PCB from the plate and place the plate on a flat surface.
Pop the smooth rods, with linear bearings attached, back into the plastic parts. 
The rod with two linear bearings on it should go on the side where the motor pulley is.
Place the entire assembly, upside down, onto the plate. Align it so the smooth rods are parallel to the plate edges and the assembly is approximately centered.
Position the two linear bearings that share a rod so that they are both in the middle third of the plate.
Position the last linear bearing so it's between the other two.
Mark each linear bearing holder mounting hole.
Drill all the holes and screw the linear bearing holders in with the wood screws.
Place one end of the belt into the belt clamp. Run the belt along its path over the pulley and idler and back to the belt clamp. 
Place the belt clamp in the middle of the plate along the belt path.
Mark and drill the belt clamp mounting holes and screw the belt clamp down.
Pull the belt tight and place the end into the belt clamp. Your Y axis is done.

===Assemble the frame (P1)===
The frame can be either one custom-cut plate or a box section composed of several precut pieces (you can have them cut to size at the hardware store).
If you have a custom-cut plate, skip this step and move on to the Z axis below.

Other parts needed:
-6 45x10cm 12mm plate (18"x4" 1/2" thick plate for you non-metric people)
-1 47.5x10cm 12mm plate (19"x4" 1/2" thick) (optional, needed only if you want to mount a spool on top of the machine.)
-Box of 3.5x20mm wood screws
Tools needed
-Drill with 3mm or 3.2mm bit
-Countersink bit
-Screwdriver or power screwdriver to match the wood screws
-Clamps (optional but highly recommended, can be replaced by helpful friend)
-Pencil
-A shim/spacer, 3mm wide

Place two of the 45x10 plates against each other on a flat surface, one standing up. 
Make sure the ends are aligned exactly by pressing another plate against them. Clamp them down in this position (or have your friend hold them).
Drill through the plate that is standing up into the side of the plate that is lying on the table, approximately halfway along the length of the plate. 
Countersink the hole and add a screw. Add two more screws about 3cm from each end of the plate.
Repeat this for another pair of plates.
Lay the two pairs on the table and put another 45x10 plate between them. Align the new plate with one of the edges.
Clamp the plates down and use 6 screws to attach the cross plate to the two corners.
Place the 3mm spacer on the table, and put the last remaining 45x10 on top of it.
Stand the remaining plates on end, and place them on top of the new plate. Use 8 screws to secure the bottom plate to the rest of the frame.
If you want to, place the 47.5x10 plate on top of the entire structure and attach it with 6 screws. This is a convenient place to mount accessories, such as a filament roll holder.

===Assemble the Z axis(P1)===

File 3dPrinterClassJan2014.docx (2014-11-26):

# Build your very own desktop 3D printer... and learn how to use it!

A kit containing all materials and software will be provided to build and operate a 3D Printer. The printer is a Graber i3, based on the Prusa i3, with nearly all of the parts being laser cut.

There will be four scheduled class dates, every Saturday from 10:00am until 2:00pm, January 11th through February 1st. More will be added if needed. The first class will focus on assembling the frame. The second will be installing the electronics. The third will cover installing the firmware and host software (Repetier will be provided) and calibration. The last class will cover importing models, slicing, printing, and troubleshooting.

Included with the kit:

- 1/4" MDF laser cut frame and hardware
- Sanguish 1.1 electronics board, with stepper drivers
- 0.35mm J-Head hot end (extruder nozzle)
- 5x stepper motors
- Heated Build Platform with glass cover

What's not included:

- 12 volt power supply. You'll need to provide a minimum 250 watt PC power supply, or purchase one online. I did not include this as it can be a good cost savings if you want to repurpose an old PC power supply. If you request it I can include one for an extra $35.
- A laptop. You will need to bring a laptop to load the firmware, calibrate the movement, and run your print jobs. I've used an old 800MHz netbook with good success, so yours doesn't need to be anything special.

# Agenda

Day 1 - Orientation and Frame assembly.

Day 2 - Electronics and motors.

Day 3 - Installing firmware and software, calibration.

Day 4 - Importing models, slicing, printing, and troubleshooting.

Day 5 (optional)

# Description of Printer

The RepRap - Open Source self-replicating machine. Uses FDM, fused deposition modeling.

The RepStrap - Similar to RepRap except mainly non-printable.

Vitamins - Anything not printed or specifically generated, i.e. nuts and bolts, bearings, rod, and threaded rod.

3 Axis’s of motion - X, Y, and Z.

Stepper Motors

Extruder - Delivers the plastic to the print bed. Consists of a cold and hot end.

- Cold end - Has a stepper and toothed shaft to push plastic to the hot end.
- Hot end - Has an orifice that once the heating element heats the plastic in a reservoir it is then squeezed out of and onto the print bed.

Build platform - The area that the plastic is extruded onto creating your model. Can be heated or not. Heated beds are best used with ABS to prevent the model from lifting or warping.

Types of plastic - PLA (Polylactic acid) and ABS (Acrylonitrile butadiene styrene) are the two most commonly used, but there are many more materials available and more coming to market.

- PLA - Is a biodegradable plastic derived from corn starch. It has a lower melting point, is harder and more brittle. It’s not UV resistant and will warp in warm temperatures. It’s very forgiving for the beginning 3D enthusiast.
- ABS - Is a petroleum based plastic and is very widely used. It has a higher melting point, is more durable as it’s not as brittle. The parts tend to be more resilient.

Models: STL files - any 3D model you create must be exported or converted to an STL file.

CAD/CAM Software

- OpenSCAD - Freeware, is a code based 3D modeling software.
- SketchUp - Freeware, with paid versions available, is a visual 3D modeling software that is widely used and supported.
- Blender - Freeware, used for many 3D applications including animation.
- FreeCAD - Freeware, I don’t know much about this.
- 123D Design - A free Autodesk product, very limited in capabilities compared to thier other products. Is specifically aimed at the maker community, included in a suite of 123D programs.
- AutoCAD - Autodesk product, expensive but very robust modeling software. Does not do organic forms easily.
- 3DS Max - Autodesk product, aimed more at animation and 3D rendering, it’s very complex with many options. Modeling can be difficult at first but results are very good.
- Solidworks - A mechanical engineering software that can be used to build a virtual mechanism to test functionality before exporting individual pieces for printing.

3D Scanning

- 123D Catch - Part of the Autodesk 123D suite. Takes a series of photos and stitches them together to generate a model you can print.
- Xbox Kinect - Uses stereoscopic imaging to scan an object. Other similar tools are on the market.
- Other forms of scanning include some laser and camera based options that can be DIY’d or purchased.

Slicing - Takes your STL file and generates G-code for your control software to send to your printer.

- Slic3r - Open Source, is simplified, but does offer many advanced options.
- Skeinforge - Open Source, lots of variables, some can be obscure.

Printer Control - Includes host software and the firmware that is loaded on your microcontroller. Allows you to manually control your printer as well as sending the G-code commands.

Host software

- Repetier - a package including both firmware, host software, it also has Slic3r and Skeinforge embedded.
- Pronterface - Is host software and can speak to many different firmwares.

Firmware

- Repetier
- Teacup
- Marlin
- Sprinter

Microcontrollers

G-Code

# Tools you will need

Screw Driver

Nut driver or pliers

Heat gun (optional)

Soldering Iron (If building electronics)

Solder

Solder wick (For cleanup of SMT components)

# Bill of Materials

To build a Graber i3 you will need the following hardware, my sources are in parentheses:

- Laser cut Frame - 1/4” or 6mm (MDF from Home Depot, 24x48 panel)
- 5x stepper motors - 40 N-cm (56 oz-in) recommended. (Steven Wilcoxon, TCM member)
- Sanguish Electronics w/ stepper drivers (bryanandaimee@gmail.com, or any other suitable 3D printer electronics platform)
- 12V Power Supply - 30A recommended if using a heated bed (old PC or Ebay)
- 2x belts - 6mm or smaller width, approx 1 meter each. (Ebay, with pulleys)
- 5x 608zz bearings (Ebay)
- 10x LM8UU linear bearings (Ebay)
- Extruder hot end (hotends.com)
- Extruder body (I printed them , but are available on Ebay)
- Endstops - mechanical or optoelectronic. (Steven Wilcoxon)
- 6x Springs for extruder and bed (AliExpress.com, but Ebay has them too)
- 2x 11.5” Threaded rod - 10-24 or 5mm (Menards)
- 6x 8mm smooth rod. 2x 12.5”, + 2x 13.5”, 2x 15.75” (Use-Enco.com)
- Heated Build Platform -optional for PLA (Ebay)
- 8”x8” glass - HBP cover (Ace Hardware)
- Nuts and bolts - #6-32 (41x ¾”, 6x ½”, 2x 1”, 4x 1¼ ”, 8x 1¾”) , M3 (20x 10mm, 4x 25mm, 4x 20mm) (Menards and McMaster-Carr.com)
- Software and firmware (Repetier.com)

Our kit includes all of the above, excluding the power supply unit, as these can be sourced for free out of old PCs. If you wish to purchase one they are available for about $25 online.

The electronics included in the kit are capable of driving a 3A load, but are configured for 2A to avoid heat issues. The electronics use the MCP2200 USB-to-Serial chip to interpret commands to the microcontroller chip, this requires a hardware driver (included in the kit) to be loaded onto your computer. The Microcontroller chip is essentially an Arduino without the board and any firmware modifications can be done through the Arduino programming environment.

# Assembly Instructions

Day 1 - Frame construction

Layout materials by session

Clean your work area

http://twelvepro.com/news/?page_id=39

Assemble the main frame:

1. Attach brackets (H) to left and right Z- axis stepper motor mounts (G). Chamfered corner will be the front outside corner.
2. Attach the Z motor mounts to the main upright. (F)
3. Attach the left and right uprights (B) to the base. (A) Orient the base such that the two square holes near the middle are facing the front.
4. Put the Y-axis motor mount (K) into the square hole on the rear of the base, and the Y-axis idler brackets (L) in the front of the base.
5. Attach front (D) and rear (E) faces.
6. Slide the main upright into position and secure to the left and right uprights.
7. Insert 2” threaded rod with 608zz bearing into the idler brackets and secure with nuts.
8. Attach Y-axis rod stops to front and back faces. Use one bolt in the bottom hole.
9. Install Z and Y-axis motors.

Assemble Y-axis and print bed:

1. Attach the two belt brackets (P) to the Y-carriage base (M).
2. Attach three linear bearings using zip ties.
3. Insert Y-axis rods and set in base.
4. Secure Y-axis rods to rod stops using zip ties.
5. Insert thermistor leads into teflon sleeves or wrap in kapton tape.
6. Solder 20-24 Ga wire to leads.
7. Add thermistor to heated build platform, leave plenty of tail to reach the control board later.
8. Solder LED(s) and resistor to board for power indicator.
9. Solder 18-20 Ga wire to contacts, leave enough tail to reach control board later.
10. Attach the heated build platform (HBP) to the Y-carriage base using three or four M3-25 screws with springs inserted between the bed and the carriage. Make firm but not tight.

Assemble X-axis Motor Mount:

1. Place the Y-axis motor mount (Y) on a level surface.
2. Insert two the rod spacers (Q), large tab down, in the two large slots near the middle.
3. Insert X-axis motor bearing plate (X) into the X-motor mount sides (Z).
4. Insert the X-motor mount sides (Z) onto the .motor mount (Y).
5. Insert Z-axis nut into outside facing recess and cover with (AA).
6. Insert two LM8UU bearings in slot.
7. Install X-axis motor mount top (W) and secure with 1¾” bolts.

Assemble X-axis Idler:

1. Place the Y-axis idler base (T) on a level surface.
2. Insert two the rod spacers (Q), large tab down, in the two large slots near the middle.
3. Insert X-axis idler bearing plate (S) into the X-idler sides (U).
4. Insert the X-idler sides (U) onto the Idler mount (T).
5. Insert Z-axis nut into outside facing recess and cover with (V).
6. Insert two LM8UU bearings in slot.
7. Install X-axis idler top (R) and secure with 1¾” bolts.

Assemble the X-carriage:

1. Place X-carriage base (N2) on a level surface.
2. Insert three LM8UU bearings.
3. Install X-carriage top (N1) and secure with 1¼” bolts.

Assemble X and Z-axis:

1. Slide 15.75” smooth rod into X-carriage bearings.
2. Determine correct orientation.
3. Insert X-carriage assembly into X-idler assembly
4. Insert X-carriage assembly into X-motor mount assembly.
5. Slide 12.5” smooth rod into X-axis motor mount bearings and X-axis idler.
6. Insert 11.5” #10-24 threaded rod into the captured nuts on the motor mount and idler assemblies.
7. Insert assembly into the rod holes on Z-motor mounts (G).
8. Attach left and right Z-axis rod holders (I).
9. Using ½” length of tubing attach the threaded rod to Z-axis motors.
10. Mount X-axis motor.

Extruder assembly:

1. Insert two 608zz bearings into recesses on extruder body.
2. Using 20mm (¾”) threaded rod or smooth rod place 608zz bearing into extruder idler.
3. mount idler to extruder body.
4. Mount extruder motor, keep loose.
5. Install small gear
6. Insert hobbed bolt into big gear.
7. Insert hobbed bolt and big gear into body. Use washers to get correct spacing for good gear alignment. Use nylock or jam nuts to secure hobbed bolt in place.
8. Make sure the gears have good contact and tighten motor.
9. Attach extruder assembly to X-carriage.

Attach belts:

1. Make sure Y-motor is loose.
2. Attach one end of the belt to the Y-carriage bolt on (P) by folding over and zip tying in place.
3. Run Y-axis belt through idler, around Y-motor pulley and back to Y-carriage.
4. Attach end of belt as above. Make sure it’s taught.
5. Tighten belt by adjusting Y-motor before tightening motor mount bolts.
6. X-carriage is similar to above.

Day 2 - Electronics

Layout materials by session

Clean your work area

http://reprap.org/wiki/Sanguish

Assemble the board:

1. Follow instructions on wiki.

Install drivers, software and firmware:

1. Download and install MCP2200 installation utility, or just the driver, your choice.
2. Install Arduino software. The latest versions might compile a little differently and may cause errors. Try it and see, if you get an error install 1.0.x, as it’s known to work without issue.
3. Install Repetier Host. This includes Slic3r and Skeinforge.
4. If your microcontroller doesn’t already have it, or you just don’t know, download the latest firmware update. The online tool works.

Verify you can talk to the microcontroller:

1. Apply 12VDC power to the board.
2. Plug in mini-USB cable.
3. Open Repetier host software.
4. Make sure you’re communicating on the right COM port and at 115200 baud rate.
5. Click the Connect button.
6. From Settings menu check to see if EEPROM parameters are populating.
7. Go to the Manual Control tab and send a command. You could hook up a motor and try sending movement commands.

*If your status line says “6 Commands waiting” you’re having communications issues and you’re not communicating with the ATMega IC.

Assemble the Hotend and Extruder:

Your hotend should be assembled with the exception of the heating resistor and the thermistor.

1. Using refractory cement or fireplace mortar, spread a little bit on the body of the resistor and insert into the large hole on the brass portion of the hotend.
2. Make sure refractory cement is covering both ends of the hole.
3. Smooth and let set up for a few hours.
4. Insert the thermistor and resistor leads into teflon sleeves or wrap in kapton tape.
5. Solder 18-20 Ga leads to the resistor and 20-24 ga leads to the thermistor. Use heatshrink to protect the leads from being shorted.
6. Buy or make a hobbed bolt.
  a. Mount extruder stepper with small gear to extruder body
  b. Put large gear on bolt with bolt head in gear recess
  c. Insert through 608zz bearings and add washers as needed to line up gears
  d. mark bolt where it lines up with the 3mm hole to the hotend.
  e. mount bolt in drill chuck, a drill press also works well
  f. using a small round file start the drill and file a shallow groove
  g. Mount a #6-32 tap into a drill press
  h. Using 2 608zz bearing on either end of the bolt hold the bolt firmly against the tap with the tap aligned on the groove. The bearings allow it to rotate as teeth are being cut into the groove.
7. Assemble the extruder body, use either a nylock nut or a jam nut to hold the hobbed bolt in place.
8. Insert a 20mm piece of rod through a 608zz bearing and place in idler
9. Tap the idler pivot holes for a 1-1/4” #6-32
10. Use 2x 1-3/4” or 2” #6-32 bolts with springs through the top of the idler assembly to nuts on the main extruder body.
11. Insert hotend into base of extruder body and hold in place with 2x 25mm bolts.

Wire it all up!:

1. Route and plug in all of your motors. Double check all of your motors are plugged in correctly, being one pin off will cause damage to either the stepper driver or the processor.
2. Mount endstops and route wire accordingly. Opto endstops require the addition of a flag in order to trigger the endstop. Mounting the endstops and flags can be a creative challenge, but generally you can mount an endstop holder to the 8mm rods on each axis, the exception being the Y-axis as the bed sits too low and hits the endstop holder.
3. Route and plug in thermistors and heating element leads.

# Upgrades

Cable chain - http://www.thingiverse.com/thing:57533

Auto Leveling Bed -

LCD Display -

# Where to order supplies

Laser cut design documents can be downloaded from https://github.com/sgraber/Graber or purchased on eBay. Hack Factory members can cut their own once checked out on the cutter.

Plywood/MDF was sourced from Home Depot (Laser cutter settings vary, but The TCM laser is 90 watts. The settings I use are Focus 68mm, Speed 30, Power 100, one pass.)

Also see: http://reprap.org/wiki/Prusa_i3_Build_Manual#Single_Sheet_Frame_Style

J-Head http://www.reprap-usa.com/index.php?route=product/product&path=60&product_id=53 (can be purchased from hotends.com)

Oven wire for connecting hotend: http://www.mcmaster.com/#8209k11/=qiucup

Kapton Tape

100k Thermistor B57560G104F or B57540G104F, From Mouser.com or Digikey.com

Teflon (PTFE) sleeving for thermistor lead insulation, McMaster Part No. 5335k11 (http://www.mcmaster.com/) (or equivalent)

HeatBed: http://www.amazon.com/gp/product/B00BLCW1NA/ref=oh_details_o07_s00_i00?ie=UTF8&psc=1 $19.99

Controller: http://reprap.org/wiki/User:Bryanandaimee (or direct contact: bryanandaimee@gmail.com)

Belt - Ebay

Pullies - Ebay

Small tiewraps

LM8UU Bearings - Ebay

608 Bearings - Ebay

Stepper motors - Ebay or TCM member Steven Wilcoxon

Threaded Rod, 10/24x36" @$2.18, Home Depot.

Machine Screws,

- 100 pack /w nuts, 3/4" #6-32 @3.99, Menards.
- 1/2 ” #6-32, Menards
- 1” #6-32, Menards
- 1-1/4” #6-32, Mcmaster Carr
- 1-3/4” #6-32, Mcmaster Carr
- 10mm M3, Mcmaster Carr
- 20mm M3, Mcmaster Carr
- 25mm M3, McMaster Carr

1/4" vinyl tubing, 10ft @1.40, Home Depot

or 1/4" poly tubing, 25' @ 3.00, Home Depot

Hobbed Bolt - 5/16”x 2”(?) or 8mm hex bolt with nylock nut or 2 nuts as jam nuts.

PC Power Supply

How to mod the power supply

or http://www.amazon.com/gp/product/B007KG0ZYI/ref=oh_details_o05_s02_i05?ie=UTF8&psc=1 $29.96

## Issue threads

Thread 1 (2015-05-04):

Y Axis endstop

paenian, 2015-05-04:
Current Y axis endstop cuts off a corner of the bed.  This isn't ideal.

paenian, 2015-05-04:
Current fix is to route bed around endstop - it sort of works.

Fix remains open.

paenian, 2015-05-04:
Next fix: attach endstop underneath, to interface with bearing under rod.
1. Design endstop mount held on by zip tie.
2. Test.

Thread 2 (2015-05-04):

Y Tensioner works poorly, requires 1/2" screws

paenian, 2015-05-04:

paenian, 2015-05-04:
First eliminated the old tension system - moving the motor - which allows the use of 3/4" screw attachment.

paenian, 2015-05-04:
Creating new issue for front mount.

Closed 2015-05-04.

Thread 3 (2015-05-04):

Replace Y idler mount with tensioning mount

paenian, 2015-05-04:

paenian, 2015-05-05:
Printed and in test - need to lasercut new front plate to fit.

paenian, 2015-05-22:
Printed, tested and working.

Closed 2015-05-22.

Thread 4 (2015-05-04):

Replace Y belt clamps with printed belt holder

paenian, 2015-05-04:

paenian, 2015-05-05:
Printed and tested - works well.

Closed 2015-05-05.

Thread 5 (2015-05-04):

Replace extruder clamp system

paenian, 2015-05-04:
Current system is prone to breakage and hard to install.

Move to a slot system - two part clamp, but side-to-side instead of top down.

Requires slots for the Bowden tube, as well as supports to hold it in.

Use two 20mm M3 screws to clamp on.

paenian, 2015-05-22:
Using a zip tie to mount the hotend & its associated bowden tube.  Seems robust so far.

Closed 2015-05-22.

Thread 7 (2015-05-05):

Modify motor clamp, add induction mount to it

paenian, 2015-05-05:

paenian, 2015-05-22:
This won't work, the hotend is too long - need the clamp for the induction sensor to be below the motor clamp.

Current plan is to mount motor on the right side of the X-Carriage w/existing clamp, and mount the induction sensor on the left side.

Closed 2015-05-22.

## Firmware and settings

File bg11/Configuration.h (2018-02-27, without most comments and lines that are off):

#define CONFIGURATION_H
#define CONFIGURATION_H_VERSION 010107
#define STRING_CONFIG_H_AUTHOR "(paenian, Nova I3)" // Who made the changes.
#define SHOW_BOOTSCREEN
#define STRING_SPLASH_LINE1 SHORT_BUILD_VERSION // will be shown during bootup in line 1
#define STRING_SPLASH_LINE2 STRING_CONFIG_H_AUTHOR         // will be shown during bootup in line 2
#define SERIAL_PORT 0
#define BAUDRATE 115200
  #define MOTHERBOARD BOARD_MKS_13
#define CUSTOM_MACHINE_NAME "Nova I3 BG11"
#define EXTRUDERS 1
#define DEFAULT_NOMINAL_FILAMENT_DIA 1.75
#define POWER_SUPPLY 0
#define TEMP_SENSOR_0 5
#define TEMP_SENSOR_1 0
#define TEMP_SENSOR_2 0
#define TEMP_SENSOR_3 0
#define TEMP_SENSOR_4 0
#define TEMP_SENSOR_BED 1
#define DUMMY_THERMISTOR_998_VALUE 25
#define DUMMY_THERMISTOR_999_VALUE 100
#define MAX_REDUNDANT_TEMP_SENSOR_DIFF 10
#define TEMP_RESIDENCY_TIME 10  // (seconds)
#define TEMP_HYSTERESIS 4       // (degC) range of +/- temperatures considered "close" to the target one
#define TEMP_WINDOW     2       // (degC) Window around target to start the residency timer x degC early.
#define TEMP_BED_RESIDENCY_TIME 10  // (seconds)
#define TEMP_BED_HYSTERESIS 3       // (degC) range of +/- temperatures considered "close" to the target one
#define TEMP_BED_WINDOW     2       // (degC) Window around target to start the residency timer x degC early.
#define HEATER_0_MINTEMP 5
#define HEATER_1_MINTEMP 5
#define HEATER_2_MINTEMP 5
#define HEATER_3_MINTEMP 5
#define HEATER_4_MINTEMP 5
#define BED_MINTEMP 5
#define HEATER_0_MAXTEMP 325
#define HEATER_1_MAXTEMP 325
#define HEATER_2_MAXTEMP 325
#define HEATER_3_MAXTEMP 325
#define HEATER_4_MAXTEMP 325
#define BED_MAXTEMP 150
#define PIDTEMP
#define BANG_MAX 255     // Limits current to nozzle while in bang-bang mode; 255=full current
#define PID_MAX BANG_MAX // Limits current to nozzle while PID is active (see PID_FUNCTIONAL_RANGE below); 255=full current
#define PID_K1 0.95      // Smoothing factor within the PID
  #define PID_FUNCTIONAL_RANGE 10 // If the temperature difference between the target temperature and the actual temperature
  #define  DEFAULT_Kp 17.45
  #define  DEFAULT_Ki 1.10
  #define  DEFAULT_Kd 69.04
#define MAX_BED_POWER 255 // limits duty cycle to bed; 255=full current
#define PREVENT_COLD_EXTRUSION
#define EXTRUDE_MINTEMP 170
#define PREVENT_LENGTHY_EXTRUDE
#define EXTRUDE_MAXLENGTH 200
#define THERMAL_PROTECTION_HOTENDS // Enable thermal protection for all extruders
#define USE_XMIN_PLUG
#define USE_YMIN_PLUG
#define USE_ZMIN_PLUG
#define ENDSTOPPULLUPS // Comment this out (using // at the start of the line) to disable the endstop pullup resistors
#define X_MIN_ENDSTOP_INVERTING false // set to true to invert the logic of the endstop.
#define Y_MIN_ENDSTOP_INVERTING false // set to true to invert the logic of the endstop.
#define Z_MIN_ENDSTOP_INVERTING true // set to true to invert the logic of the endstop.
#define X_MAX_ENDSTOP_INVERTING false // set to true to invert the logic of the endstop.
#define Y_MAX_ENDSTOP_INVERTING false // set to true to invert the logic of the endstop.
#define Z_MAX_ENDSTOP_INVERTING false // set to true to invert the logic of the endstop.
#define Z_MIN_PROBE_ENDSTOP_INVERTING false // set to true to invert the logic of the probe.
#define DEFAULT_AXIS_STEPS_PER_UNIT   { 80, 80, 4000, 155 }
#define DEFAULT_MAX_FEEDRATE          { 300, 300, 5, 50 }
#define DEFAULT_MAX_ACCELERATION      { 3000, 3000, 100, 10000 }
#define DEFAULT_ACCELERATION          1000    // X, Y, Z and E acceleration for printing moves
#define DEFAULT_RETRACT_ACCELERATION  3000    // E acceleration for retracts
#define DEFAULT_TRAVEL_ACCELERATION   3000    // X, Y, Z acceleration for travel (non printing) moves
#define DEFAULT_XJERK                  5.0
#define DEFAULT_YJERK                  5.0
#define DEFAULT_ZJERK                  0.3
#define DEFAULT_EJERK                  5.0
#define Z_MIN_PROBE_USES_Z_MIN_ENDSTOP_PIN
#define FIX_MOUNTED_PROBE
#define X_PROBE_OFFSET_FROM_EXTRUDER -30  // X offset: -left  +right  [of the nozzle]
#define Y_PROBE_OFFSET_FROM_EXTRUDER 12  // Y offset: -front +behind [the nozzle]
#define Z_PROBE_OFFSET_FROM_EXTRUDER -1   // Z offset: -below +above  [the nozzle]
#define XY_PROBE_SPEED 8000
#define Z_PROBE_SPEED_FAST HOMING_FEEDRATE_Z
#define Z_PROBE_SPEED_SLOW (Z_PROBE_SPEED_FAST / 2)
#define Z_CLEARANCE_DEPLOY_PROBE   5 // Z Clearance for Deploy/Stow
#define Z_CLEARANCE_BETWEEN_PROBES  5 // Z Clearance between probe points
#define Z_PROBE_OFFSET_RANGE_MIN -20
#define Z_PROBE_OFFSET_RANGE_MAX 20
#define X_ENABLE_ON 0
#define Y_ENABLE_ON 0
#define Z_ENABLE_ON 0
#define E_ENABLE_ON 0 // For all extruders
#define DISABLE_X false
#define DISABLE_Y false
#define DISABLE_Z false
#define DISABLE_E false // For all extruders
#define DISABLE_INACTIVE_EXTRUDER true // Keep only the active extruder enabled.
#define INVERT_X_DIR false
#define INVERT_Y_DIR false
#define INVERT_Z_DIR false
#define INVERT_E0_DIR false
#define INVERT_E1_DIR false
#define INVERT_E2_DIR false
#define INVERT_E3_DIR false
#define INVERT_E4_DIR false
#define X_HOME_DIR -1
#define Y_HOME_DIR -1
#define Z_HOME_DIR -1
#define X_BED_SIZE 200
#define Y_BED_SIZE 200
#define X_MIN_POS 0
#define Y_MIN_POS 0
#define Z_MIN_POS 0
#define X_MAX_POS X_BED_SIZE
#define Y_MAX_POS Y_BED_SIZE
#define Z_MAX_POS 200
#define MIN_SOFTWARE_ENDSTOPS
  #define MIN_SOFTWARE_ENDSTOP_X
  #define MIN_SOFTWARE_ENDSTOP_Y
  #define MIN_SOFTWARE_ENDSTOP_Z
#define MAX_SOFTWARE_ENDSTOPS
  #define MAX_SOFTWARE_ENDSTOP_X
  #define MAX_SOFTWARE_ENDSTOP_Y
  #define MAX_SOFTWARE_ENDSTOP_Z
#define AUTO_BED_LEVELING_BILINEAR
  #define ENABLE_LEVELING_FADE_HEIGHT
  #define SEGMENT_LEVELED_MOVES
  #define LEVELED_SEGMENT_LENGTH 5.0 // (mm) Length of all segments (except the last one)
  #define G26_MESH_VALIDATION   // Enable G26 mesh validation
    #define MESH_TEST_NOZZLE_SIZE     0.4   // (mm) Diameter of primary nozzle.
    #define MESH_TEST_LAYER_HEIGHT    0.2   // (mm) Default layer height for the G26 Mesh Validation Tool.
    #define MESH_TEST_HOTEND_TEMP   205.0   // (°C) Default nozzle temperature for the G26 Mesh Validation Tool.
    #define MESH_TEST_BED_TEMP       60.0   // (°C) Default bed temperature for the G26 Mesh Validation Tool.
  #define GRID_MAX_POINTS_X 3
  #define GRID_MAX_POINTS_Y GRID_MAX_POINTS_X
  #define LEFT_PROBE_BED_POSITION 30
  #define RIGHT_PROBE_BED_POSITION 170
  #define FRONT_PROBE_BED_POSITION 30
  #define BACK_PROBE_BED_POSITION 170
  #define MIN_PROBE_EDGE 10
#define Z_SAFE_HOMING
  #define Z_SAFE_HOMING_X_POINT ((X_BED_SIZE) / 2)    // X point for Z homing when homing all axes (G28).
  #define Z_SAFE_HOMING_Y_POINT ((Y_BED_SIZE) / 2)    // Y point for Z homing when homing all axes (G28).
#define HOMING_FEEDRATE_XY (50*60)
#define HOMING_FEEDRATE_Z  (5*60)
#define EEPROM_SETTINGS // Enable for M500 and M501 commands
#define EEPROM_CHITCHAT   // Give feedback on EEPROM commands. Disable to save PROGMEM.
#define HOST_KEEPALIVE_FEATURE        // Disable this if your host doesn't like keepalive messages
#define DEFAULT_KEEPALIVE_INTERVAL 2  // Number of seconds between "busy" messages. Set with M113.
#define BUSY_WHILE_HEATING            // Some hosts require "busy" messages even during heating
#define PREHEAT_1_TEMP_HOTEND 180
#define PREHEAT_1_TEMP_BED     70
#define PREHEAT_1_FAN_SPEED     0 // Value from 0 to 255
#define PREHEAT_2_TEMP_HOTEND 200
#define PREHEAT_2_TEMP_BED    110
#define PREHEAT_2_FAN_SPEED     0 // Value from 0 to 255
#define PRINTJOB_TIMER_AUTOSTART
#define PRINTCOUNTER
#define LCD_LANGUAGE en
#define DISPLAY_CHARSET_HD44780 JAPANESE
#define ULTRA_LCD   // Character based
#define SDSUPPORT
#define REVERSE_ENCODER_DIRECTION
#define REPRAP_DISCOUNT_SMART_CONTROLLER
#define SOFT_PWM_SCALE 0
#define SERVO_DELAY { 300 }

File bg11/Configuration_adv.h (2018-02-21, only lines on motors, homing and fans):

#define E0_AUTO_FAN_PIN -1
#define E1_AUTO_FAN_PIN -1
#define E2_AUTO_FAN_PIN -1
#define E3_AUTO_FAN_PIN -1
#define E4_AUTO_FAN_PIN -1
#define X_HOME_BUMP_MM 5
#define Y_HOME_BUMP_MM 5
#define Z_HOME_BUMP_MM 2
#define HOMING_BUMP_DIVISOR { 2, 2, 4 }  // Re-Bump Speed Divisor (Divides the Homing Feedrate)
#define MICROSTEP_MODES {16,16,16,16,16} // [1,2,4,8,16]
#define DIGIPOT_I2C_MOTOR_CURRENTS { 1.0, 1.0, 1.0, 1.0, 1.0, 1.0, 1.0, 1.0 }  //  AZTEEG_X3_PRO

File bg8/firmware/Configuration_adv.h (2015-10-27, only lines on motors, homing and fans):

#define CONTROLLERFAN_PIN -1 //Pin used for the fan to cool controller (-1 to disable)
#define EXTRUDER_0_AUTO_FAN_PIN   FAN_1_PIN
#define EXTRUDER_1_AUTO_FAN_PIN   FAN_1_PIN
#define EXTRUDER_2_AUTO_FAN_PIN   FAN_1_PIN
#define ENDSTOPS_ONLY_FOR_HOMING // If defined the endstops will only be used for homing
#define X_HOME_RETRACT_MM 5
#define Y_HOME_RETRACT_MM 5
#define Z_HOME_RETRACT_MM 2
#define MICROSTEP1 LOW,LOW
#define MICROSTEP2 HIGH,LOW
#define MICROSTEP4 LOW,HIGH
#define MICROSTEP8 HIGH,HIGH
#define MICROSTEP16 HIGH,HIGH
#define MICROSTEP_MODES {16,16,16,16,16} // [1,2,4,8,16]
#define DIGIPOT_MOTOR_CURRENT {180,180,180,180,180} // Values 0-255 (RAMBO 135 = ~0.75A, 185 = ~1A)
#define DIGIPOT_I2C_MOTOR_CURRENTS {1.0, 1.0, 1.0, 1.0, 1.0, 1.0, 1.0, 1.0}

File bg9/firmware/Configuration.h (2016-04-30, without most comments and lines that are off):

#define CONFIGURATION_H
#include "boards.h"
#define STRING_VERSION_CONFIG_H __DATE__ " " __TIME__ // build date and time
#define STRING_CONFIG_H_AUTHOR "(paenian, bg9 config)" // Who made the changes.
#define SERIAL_PORT 0
#define BAUDRATE 115200
  #define MOTHERBOARD BOARD_RAMPS_13_EFB
#define EXTRUDERS 1
#define POWER_SUPPLY 1
#define TEMP_SENSOR_0 5
#define TEMP_SENSOR_1 0
#define TEMP_SENSOR_2 0
#define TEMP_SENSOR_BED 1
#define MAX_REDUNDANT_TEMP_SENSOR_DIFF 10
#define TEMP_RESIDENCY_TIME 10  // (seconds)
#define TEMP_HYSTERESIS 3       // (degC) range of +/- temperatures considered "close" to the target one
#define TEMP_WINDOW     2       // (degC) Window around target to start the residency timer x degC early.
#define HEATER_0_MINTEMP 5
#define HEATER_1_MINTEMP 5
#define HEATER_2_MINTEMP 5
#define BED_MINTEMP 5
#define HEATER_0_MAXTEMP 325
#define HEATER_1_MAXTEMP 325
#define HEATER_2_MAXTEMP 325
#define BED_MAXTEMP 150
#define PIDTEMP
#define BANG_MAX 255 // limits current to nozzle while in bang-bang mode; 255=full current
#define PID_MAX BANG_MAX // limits current to nozzle while PID is active (see PID_FUNCTIONAL_RANGE below); 255=full current
  #define PID_FUNCTIONAL_RANGE 10 // If the temperature difference between the target temperature and the actual temperature
  #define PID_INTEGRAL_DRIVE_MAX PID_MAX  //limit for the integral term
  #define K1 0.95 //smoothing factor within the PID
  #define PID_dT ((OVERSAMPLENR * 10.0)/(F_CPU / 64.0 / 256.0)) //sampling period of the temperature routine
    #define  DEFAULT_Kp 66.93
    #define  DEFAULT_Ki 8.79
    #define  DEFAULT_Kd 127.48
#define MAX_BED_POWER 255 // limits duty cycle to bed; 255=full current
#define PREVENT_DANGEROUS_EXTRUDE
#define PREVENT_LENGTHY_EXTRUDE
#define EXTRUDE_MINTEMP 170
#define EXTRUDE_MAXLENGTH (X_MAX_LENGTH+Y_MAX_LENGTH) //prevent extrusion of very large distances.
#define ENDSTOPPULLUPS // Comment this out (using // at the start of the line) to disable the endstop pullup resistors
  #define ENDSTOPPULLUP_XMAX
  #define ENDSTOPPULLUP_YMAX
  #define ENDSTOPPULLUP_ZMAX
  #define ENDSTOPPULLUP_XMIN
  #define ENDSTOPPULLUP_YMIN
  #define ENDSTOPPULLUP_ZMIN
const bool X_MIN_ENDSTOP_INVERTING = false; // set to true to invert the logic of the endstop.
const bool Y_MIN_ENDSTOP_INVERTING = false; // set to true to invert the logic of the endstop.
const bool Z_MIN_ENDSTOP_INVERTING = true; // set to true to invert the logic of the endstop.
const bool X_MAX_ENDSTOP_INVERTING = true; // set to true to invert the logic of the endstop.
const bool Y_MAX_ENDSTOP_INVERTING = true; // set to true to invert the logic of the endstop.
const bool Z_MAX_ENDSTOP_INVERTING = true; // set to true to invert the logic of the endstop.
#if defined(COREXY) && !defined(DISABLE_MAX_ENDSTOPS)
  #define DISABLE_MAX_ENDSTOPS
#endif
#define X_ENABLE_ON 0
#define Y_ENABLE_ON 0
#define Z_ENABLE_ON 0
#define E_ENABLE_ON 0 // For all extruders
#define DISABLE_X false
#define DISABLE_Y false
#define DISABLE_Z false
#define DISABLE_E false // For all extruders
#define DISABLE_INACTIVE_EXTRUDER true //disable only inactive extruders and keep active extruder enabled
#define INVERT_X_DIR false    // for Mendel set to false, for Orca set to true
#define INVERT_Y_DIR true    // for Mendel set to true, for Orca set to false
#define INVERT_Z_DIR true     // for Mendel set to false, for Orca set to true
#define INVERT_E0_DIR false   // for direct drive extruder v9 set to true, for geared extruder set to false
#define INVERT_E1_DIR false    // for direct drive extruder v9 set to true, for geared extruder set to false
#define INVERT_E2_DIR false   // for direct drive extruder v9 set to true, for geared extruder set to false
#define X_HOME_DIR -1
#define Y_HOME_DIR -1
#define Z_HOME_DIR -1
#define min_software_endstops true // If true, axis won't move to coordinates less than HOME_POS.
#define max_software_endstops true  // If true, axis won't move to coordinates greater than the defined lengths below.
#define X_MAX_POS 205
#define X_MIN_POS 0
#define Y_MAX_POS 205
#define Y_MIN_POS 0
#define Z_MAX_POS 200
#define Z_MIN_POS 0
#define X_MAX_LENGTH (X_MAX_POS - X_MIN_POS)
#define Y_MAX_LENGTH (Y_MAX_POS - Y_MIN_POS)
#define Z_MAX_LENGTH (Z_MAX_POS - Z_MIN_POS)
#define ENABLE_AUTO_BED_LEVELING // Delete the comment to enable (remove // at the start of the line)
#define Z_PROBE_REPEATABILITY_TEST  // If not commented out, Z-Probe Repeatability test will be included if Auto Bed Leveling is Enabled.
  #define AUTO_BED_LEVELING_GRID
    #define LEFT_PROBE_BED_POSITION 40
    #define RIGHT_PROBE_BED_POSITION 180
    #define BACK_PROBE_BED_POSITION 180
    #define FRONT_PROBE_BED_POSITION 40
    #define AUTO_BED_LEVELING_GRID_POINTS 3
  #define X_PROBE_OFFSET_FROM_EXTRUDER -30
  #define Y_PROBE_OFFSET_FROM_EXTRUDER 5
  #define Z_PROBE_OFFSET_FROM_EXTRUDER -1
  #define Z_RAISE_BEFORE_HOMING 4       // (in mm) Raise Z before homing (G28) for Probe Clearance.
  #define XY_TRAVEL_SPEED 8000         // X and Y axis travel speed between probes, in mm/min
  #define Z_RAISE_BEFORE_PROBING 5    //How much the extruder will be raised before traveling to the first probing point.
  #define Z_RAISE_BETWEEN_PROBINGS 5  //How much the extruder will be raised when traveling from between next probing points
  #define Z_SAFE_HOMING   // This feature is meant to avoid Z homing with probe outside the bed area.
    #define Z_SAFE_HOMING_X_POINT (X_MAX_LENGTH/2)    // X point for Z homing when homing all axis (G28)
    #define Z_SAFE_HOMING_Y_POINT (Y_MAX_LENGTH/2)    // Y point for Z homing when homing all axis (G28)
    #if X_PROBE_OFFSET_FROM_EXTRUDER < 0
      #if (-(X_PROBE_OFFSET_FROM_EXTRUDER * AUTO_BED_LEVELING_GRID_POINTS) >= (RIGHT_PROBE_BED_POSITION - LEFT_PROBE_BED_POSITION))
	     #error "The X axis probing range is not enough to fit all the points defined in AUTO_BED_LEVELING_GRID_POINTS"
	  #endif
	#else
      #if ((X_PROBE_OFFSET_FROM_EXTRUDER * AUTO_BED_LEVELING_GRID_POINTS) >= (RIGHT_PROBE_BED_POSITION - LEFT_PROBE_BED_POSITION))
	     #error "The X axis probing range is not enough to fit all the points defined in AUTO_BED_LEVELING_GRID_POINTS"
	  #endif
	#endif
    #if Y_PROBE_OFFSET_FROM_EXTRUDER < 0
      #if (-(Y_PROBE_OFFSET_FROM_EXTRUDER * AUTO_BED_LEVELING_GRID_POINTS) >= (BACK_PROBE_BED_POSITION - FRONT_PROBE_BED_POSITION))
	     #error "The Y axis probing range is not enough to fit all the points defined in AUTO_BED_LEVELING_GRID_POINTS"
	  #endif
	#else
      #if ((Y_PROBE_OFFSET_FROM_EXTRUDER * AUTO_BED_LEVELING_GRID_POINTS) >= (BACK_PROBE_BED_POSITION - FRONT_PROBE_BED_POSITION))
	     #error "The Y axis probing range is not enough to fit all the points defined in AUTO_BED_LEVELING_GRID_POINTS"
	  #endif
	#endif
#define MANUAL_X_HOME_POS 0
#define MANUAL_Y_HOME_POS 0
#define MANUAL_Z_HOME_POS 0
#define NUM_AXIS 4 // The axis order in all axis related arrays is X, Y, Z, E
#define HOMING_FEEDRATE {50*60, 50*60, 1*60, 0}  // set the homing speeds (mm/min)
#define DEFAULT_AXIS_STEPS_PER_UNIT   {80,80,4000,155}  // default steps per unit for Ultimaker
#define DEFAULT_MAX_FEEDRATE          {500, 500, 1, 50}    // (mm/sec)
#define DEFAULT_MAX_ACCELERATION      {9000,9000,100,10000}    // X, Y, Z, E maximum start speed for accelerated moves. E default values are good for Skeinforge 40+, for older versions raise them a lot.
#define DEFAULT_ACCELERATION          3000    // X, Y, Z and E max acceleration in mm/s^2 for printing moves
#define DEFAULT_RETRACT_ACCELERATION  3000   // X, Y, Z and E max acceleration in mm/s^2 for retracts
#define DEFAULT_XYJERK                10.0    // (mm/sec)
#define DEFAULT_ZJERK                 0.25     // (mm/sec)
#define DEFAULT_EJERK                 5.0    // (mm/sec)
#define CUSTOM_M_CODES
  #define CUSTOM_M_CODE_SET_Z_PROBE_OFFSET 851
  #define Z_PROBE_OFFSET_RANGE_MIN -15
  #define Z_PROBE_OFFSET_RANGE_MAX -5
#define EEPROM_SETTINGS
#define EEPROM_CHITCHAT
#define PLA_PREHEAT_HOTEND_TEMP 180
#define PLA_PREHEAT_HPB_TEMP 70
#define PLA_PREHEAT_FAN_SPEED 255   // Insert Value between 0 and 255
#define ABS_PREHEAT_HOTEND_TEMP 240
#define ABS_PREHEAT_HPB_TEMP 100
#define ABS_PREHEAT_FAN_SPEED 255   // Insert Value between 0 and 255
#define ULTIPANEL  //the UltiPanel as on Thingiverse
  #define NEWPANEL  //enable this if you have a click-encoder panel
  #define SDSUPPORT
  #define ULTRA_LCD
    #define LCD_WIDTH 20
    #define LCD_HEIGHT 4
#define SOFT_PWM_SCALE 0
#define FILAMENT_SENSOR_EXTRUDER_NUM	0  //The number of the extruder that has the filament sensor (0,1,2)
#define MEASUREMENT_DELAY_CM			14  //measurement delay in cm.  This is the distance from filament sensor to middle of barrel
#define DEFAULT_NOMINAL_FILAMENT_DIA  3.0  //Enter the diameter (in mm) of the filament generally used (3.0 mm or 1.75 mm) - this is then used in the slicer software.  Used for sensor reading validation
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

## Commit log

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2014-10-15 Added angle and offset to the extruder mount - makes it easy to twist and shout. Updated motormount extruder, adding an angled slit courtesy of Doug.
    [1.75_bowden_tap_m5idler.stl, m5_clamp_angled.stl, mirror_1.75_bowden_tap_m5idler.stl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]
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2014-11-27 Created some aggressively minimal plans. They share many lines, basically any I could think of that wouldn't affect the parts.
    [graber2030_plate1_minimal.dxf, graber2030_plate2_minimal.dxf]
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2014-12-05 Fixed scaling.
    [graber2030_plate2_minimal.dxf]
2014-12-06 Fixed filename issues
    [graber2030_plate1_minimal.dxf, graber2030_plate2_minimal.dxf]
2014-12-14 General updates. Slight rearrangement of parts for plating, updated several parts based on current build.
    [bowden_mount.scad, dual_fan_mount.stl, dual_hotend_clamp.stl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]
2014-12-16 Edited the extruder to support the newer, longer e3d pushfits. Basically just beefed it up a tad. Increased beef on the z clamp, because I busted one. Fan and hotend mounts modified for the e3d V6; t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
    [1.75_bowden_tap_m5idler.stl, bowden_mount.scad, dual_fan_mount.stl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]
2014-12-19 Beefed up the Z clamps, cut down the fan mount for the shorter e3ds. It uses a 40mm fan still... might switch to dual 30mm later.
    [bowden_mount.scad, dual_fan_mount.stl, dual_hotend_clamp.stl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]
2014-12-19 Added the foot stl - not sure where the source went. Also added a quick dual-extrusion calibration part, because I needed one.
    [dual_calibration.scad, dual_calibration_inner.stl, dual_calibration_outer.stl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]
2015-01-03 Updates to the fan mount to accommodate the shorter e3d V5 nozzles.
    [bowden_mount.scad, dual_calibration.scad, dual_fan_mount.stl]
2015-01-03 Initial commit of i3 redesign.
    Of note:
    - new top brace replaces Z rod holders
    - Now can be cut on a 1000x600mm laser cutter as a single sheet
    - Nova Labs logo!
    - Many shared edges, for faster cutting but more annoying editing. Sorry.
    Still todo:
    Add holes for the Rumba controller on one side
    Add holes for LED power supply on the other side
    [nova2440_monoplate.dxf]
2015-01-03 New LM8UU clamps, designed to be installed from above, in case one dies or something. Like, for instance, if you ship one to your bro and suddenly realize that they're almost impossible to install af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
    They need longer screws, but no nut traps - so fewer parts.
    Install with flat or dome heads for super-low-profile mounting
    - that way you can have thinner bed, assuming you have some fancy leveler or something.
    I am currently working on a stronger design, relocated LCD (to the top) with auto leveling.
    Paul
    [lm8uu_clamp.scad, lm8uu_clamp.stl]
2015-01-03 Added mounting holes for RUMBA - holes for other electronics are still there. - Rumba's holes are a little pointy on top.
    Added mounting holes for power supply
    - PS holes are also a little pointy.
    Removed electronics mounting holes from second side.
    - Left side: electronics
    - Right side: power supply
    Cut corner off of Y bed
    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
    [nova2440_monoplate.dxf]
2015-01-03 Removed unused hole from back panel - used to be for endstop mounting.
    As far as I can tell, this is ready to cut.
    I plan to cut it out tomorrow, and will build it as soon as I can.
    Other things I might add:
    - Mount for induction sensor on X carriage
    - Holes for zip tying cables various places
    - Fan mount for electronics cooling
    [nova2440_monoplate.dxf]
2015-01-03 Fixed some tabs that were too long on the Y axis - motor mount, idler mount, and belt mount. Also added a couple velcro tie slots to the base plate.
    [nova2440_monoplate.dxf]
2015-01-03 Flipped the electronics so the stock LCD controller cables will definitely reach :-) Added a little tie slot above the electronics. Pretty sure I'll use it.
    [nova2440_monoplate.dxf]
2015-01-05 Many minor edits to the design, based on first build. No incompatibilities, just trying to ease a few frustrations.
    In rough order of importance
    -Added divot on LCD to route around top screw
    --if you cut the old one, just file a notch.
    -Added tabs on Y motor and idler mount sites
    --Old ones had issues with washer getting into gap.
    -Deeper pockets on Y Idler mounts so you can use 3/4" screws
    --Y Motor mount still needs 1/2" screws.
    -Move Power Supply up 10mm
    --clears the cable hole completely; old one was partially blocking (not really a problem).
    -M3 spacers are bigger
    -M4 spacers are bigger
    -Divot around top center washer
    --you print with your eyes first.
    [nova2440_monoplate.dxf]
2015-01-06 First pass at the induction sensor mount.
    This will be installed on my old i3 for testing.
    [induction_mount.scad, induction_mount.stl]
2015-01-15 Modded the extruder to be a bit more robust, and to take 10mm screws to reduce part count. Modded the extruder clamp to ride higher, give a bit more print height, and provide more clearance to the id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
    [1.75_groovemount_m5idler.stl, bowden_mount.scad, bowden_mount_low.stl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]
2015-01-16 Flipped the extruder clamp upside down, so the extruder points towards the bed. Sort of important, actually.
    Adjusted the LCD buttons to use the lasercut standoffs - just had to fix the reset button standoff.
    [extruder_clamp_2screw.stl, lcd_buttons.stl, lcd_mount.scad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]
2015-01-18 nova2440: Added a fan mount for the electronics Power Supply: Adjusted sizing a little bit, switched it to take 6-32 screws and square nuts.
    [PowerSupply.scad, PowerSupply.stl, nova2440_monoplate.dxf]
2015-01-18 Rounded the corners of the power supply cover - should print better/less chance of delaminating on the sides.
    [PowerSupply.scad, PowerSupply.stl]
2015-01-27 Playing with different ways to mount the induction sensor. I think that the best option thus far is to hang it off the back.
    [1.75_grooveclamp_clamp.stl, 1.75_grooveclamp_m5idler.stl, bowden_mount.scad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]
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2015-02-01 Got rid of the induction sensor mount on the clamp. It doesn't work too well right there, the e3d hotend is a bit too long.
    [1.75_grooveclamp_clamp.stl, motormount_extruder_v2.scad]
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2015-02-14 Made the endstop mount a little sleeker, added extruder to use the Mark 8 drive gear. Looks like we'll be using that instead, the mark7 is backordered.
    [1.75_mark8_grooveclamp_m5idler.stl, endstop_mount_M8.scad, endstop_mount_M8.stl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]
2015-02-20 Modified the extruder to fit the Mark 8 drive gear - since the mark 7 got backordered :-( Will test tonight.
    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
    [1.75_mark8_grooveclamp_m5idler.stl, endstop_mount_M8.scad, endstop_mount_M8.stl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]
2015-02-22 Strengthened the extruder a bit.
    [1.75_mark8_grooveclamp_m5idler.stl, motormount_extruder_v2.scad]
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2015-04-24 Adding new plates without the X axis.
    Also moved the LCD screen over more.
    [nova2440_monoplate_nox.dxf]
2015-04-24 Moved the LCD over to accommodate shorter cables.
    [nova2440_monoplate.dxf]
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2015-04-24 Added preliminary X-ends.
    The X carriage is functional, but the belt is out of place for the pulleys we're using. Will update soon.
    Both the X ends have been flipped to fit the Graber i3 - which means that the motor's now in front facing backwards, but that the extruder motor gets plenty of clearance.
    Still todo: figure out a good way to mount the induction sensor onto the carriage.
    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
    [bearing-guide.scad, bearing-holder-single-plate-y.scad, boxframe.scad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]
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2015-04-28 Fixed the X-idler end tensioner - the nut traps were all wonky.
    [x-end.scad, x-tensioner.stl, y-drivetrain.scad]
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2015-04-30 Testing out new parts for bg7. All other parts have minimal changes, if any.
    [Configuration.h, nova2440_bg7_new_parts_test.dxf]
2015-05-01 Second pass at a 4-cornered Y bed. Moved the supports to the outside, and added an exterior bump.
    Hoping to make the endstop inset shallower, but the first version (slightly too narrow) was actually quite stiff, so I'm not too worried.
    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
    [nova2440_bg7_layout.dxf, nova2440_bg7_new_parts_test.dxf, novalabs_plate.stl]
2015-05-01 Took out some cruft with the endstops, so I can make the bed wings a little bit bigger.
    [endstop_mount_M8.scad, endstop_mount_M8.stl]
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2015-05-05 Fixed an underscore.
    [y-belt.stl]
2015-05-05 Minor changes to the endstop mount. Updated the size of the Y tensioner. Added washer risers to the tensioners. Fixed scaling issue with M3 nuts. Adjusted lasercut files to accommodate new tensioner,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
    [endstop_mount_M8.scad, endstop_mount_M8.stl, metric.scad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]
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2015-05-14 Final update of the lasercutter files.
    Modified the extruder - no more clamp plate, hold the hotend in with zip ties :-)
    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
    [motormount_ext_bg7.stl, motormount_extruder_v2.scad, nova2440_bg7_layout.dxf]
2015-05-22 Updating the rest of the X axis.
    New lasercut files just mess with the cut colors to make the lasering happier.
    New extruder_mount.scad & stl are the mounts from within the motormount_extruder_v2, modified to fit the new X carriage. This is all work-in-progress, test printing now.
    Updated new x carriage, added a mounting hole to secure the extruder vertically. The two 20mm holes will be used to mount the induction sensor in front.
    Updated fit on X-ends.
    [conf_bushing.scad, extruder_mount.scad, extruder_mount.stl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]
2015-05-22 New Z clamps. Printing now - the cutout's there so I can see if you guys actually installed 'em correctly.
    [z_clamp.scad, z_clamp.stl]
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2015-07-10 Corrected values to match the BG7 printers.
    [Configuration.h]
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2015-09-11 Test object for z-strength metering. Mark the item well, then pull till it snaps.
    [BlackRose.dxf, Letters.dxf, Write.scad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]
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2015-09-12 Updated the endstop mount - works well now. Minor updates to the frame, adding keyed slots various places, moving the electronics up a tad.
    Still todo: fan mount?! Can we mount the fan to the U frame instead, not bother with the separate mount?
    Other than that... need to test all the parts, then plate & print? Can't think of anything else missing.
    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
    [endstop_mount.stl, endstop_mount_2.scad, nova2440_bg8_layout.dxf]
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2015-09-19 Bugfix on the LCD mount holes; minor edit to Y motor mount.
    Also updated the y-belt, added better nut traps.
    [full_plate.stl, induction_mount.scad, induction_mount.stl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]
2015-09-24 Updated full plate - had the wrong extruder mount on there.
    Also updated the extruder mount to have three screwholes - so that you can use the clamp if you convert your machine to a Bowden extruder later.
    [extruder_mount.scad, extruder_mount.stl, full_plate.stl]
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2015-09-30 Fixed screwhole on x-carriage, and cap holes on the tensioners. Replated with new pards.
    [full_plate.stl, small_plate.stl, tall_plate.stl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]
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2015-10-03 Added lasercut files for the frames, ready for Mongo to burn.
    [nova2440_bg8_layout_and_test_corners.dxf]
2015-10-07 The start of a fan mount. Hilariously, the main thing missing is the actual fan mount. Plan is to use offsets to push this back from the fan mounting lugs, and have two long screws going through fan-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
    [fan_mount.scad]
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2015-10-08 Forgot a subtraction on my air path :-( So the wall gets infinitely thin towards the top! Simple fix, just wished I'd noticed before I started the test print.
    [fan_mount.scad, fan_mount.stl]
2015-10-13 Updated fan mount, fits the height much better.
    Usable now, but you need really long m3 screws.
    Debating redesign, move fan down a bit, add independent mounting screwholes.
    [fan_mount.scad, fan_mount_2.stl]
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2016-01-11 Made a new dual extruder mount
    extruders+induction sensor :+1:
    This is designed to mount on either of the two sets of screws on the X
    carriage.
    Preferably the 20mm side... and it should have enough clearance to mount
    the standard e3d fan ducts.
    Next step is to use the other screw(s) to make a print cooling fan mount
    :8ball:
    [bowden_mount.scad, dual_mount_20mm.stl, dual_mount_30mm.stl]
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2016-01-20 Had to raise the screwholes on the x carriage, and therefore drop the hotend mount so they'll reach the bed.
    I used the old measurements in my Bertha file; they were for the e3d v5 :-( The v6 is shorter enough to matter a bit.
    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
    [bowden_mount.scad, dual_mount_30mm_dropped.stl]
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2016-02-12 Minor updates, sides of the duct are closed, fan mount is angled for clearance.
    I still need to design a clip-in mount for the fan, and a way to mount the duct to the hotends and/or carriage.
    Idea: Use a thick-ish band to connect to all three of the hotend mounting holes, thus moving the hotends towards the front of the printer. We've got a little room there, anyways. Not sure if the 20mm screws will be long enough, though.
    [bowden_fan_mount.stl, fan_mount.scad]
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2016-02-14 Dual-extruder cooler for the i3.
    'tis a thing of beauty. The blower is canted at a rakish (-5 degree) angle and just slots right in - airflow is uniform and spot on... and everything has like, 1mm of clearance. Plus it kind of looks like a claw, and makes it nearly impossible to burn yourself on the hotends :-)
    You might need longer m3 screws for mounting - the stock is 20mm, dome-head socket cap screws. On my carriage update, I did sink the nuts in a bit more and it fits for me. No reason to use the new carriage, although the upper screw mounts won't hurt you. Odds are good I'll mount something there, just because it annoys me that they're unused.
    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
    [bowden_fan_mount.stl, fan_mount.scad]
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2016-02-27 Modification to the inline Bowden mount courtesy of Zack.
    Moved the induction sensor over 7mm, to avoid interference with the hotends - there was inconsistent sensing at temperature, either due to overheated sensor or the hotend's EMF.
    The sensor is now [-30,1]mm from the nozzle.
    [bowden_mount.scad, hotend_fan_mount.stl, inline_bowden_mount.stl]
2016-03-08 Fixed issue with fan_mount.scad
    [fan_mount.scad]
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2016-03-11 Full up test of inverted power supply mount.
    Going to go lasercut it now :-)
    [nova2440_bg9_layout.dxf]
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2016-04-06 quick layout of upgrade parts for new PS mount
    If you really want the new power supply mount, lasercut this & then swap
    out all the parts. Unfortunately, it includes most of the big parts :-(
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2016-04-21 Updated for cutting - measured the parts, fixed the scad a tiny bit. Then cut! And it all fits perfectly!
    [base_plate.dxf, endcap.scad, foot_plate.dxf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]
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2017-02-01 Updated extruder - better clamp
    todo: Print and test this guy
    add the holes for the new electronics to the frame
    update extruder motor clamp - needs more clearance on the corners
    update fan mount - change from exhaust fan to blower
    [cooling_fan_mount.scad, extruder_mount.scad, motormount_extruder_v2.scad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]
2017-02-01 embiggened extruder mount, ducted fan cooler
    ducted fan cooler probably needs work - pretty sure the fan'll run into
    the Z axis on the right side, since I didn't model it.
    [cooling_fan_mount.scad, cooling_fan_mount.stl, extruder_mount.scad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]
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2017-02-12 Updated x-end motor
    Now both the idler and motor can have a spring, to make the ends into anti-backlash nuts. Normal usage is one nut; this uses gravity to hold the x-end on. Advanced usage is two nuts & a spring - which holds the carriage down. Not recommended for the beginner - a head crash with anti-backlash nuts will break something badly.
    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
    [full_plate.stl, x-axis_plate.stl, x-end.scad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]
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2017-03-24 Added MKS documentation, and TFT docs.
    Worried that I won't be able to find them again :-)
    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
    [spool_roller.scad, top_spool_roller.stl]
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2017-07-09 Fixed issue with duplicate extension.
    [x-tensioner_for_metal_toothed_idler.stl]
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2017-11-21 Redid the extruder... was missing a screw!
    [motormount_extruder_v2.scad, motormount_extruder_v2.stl, spool_bearing.scad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]
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2018-02-21 Added firmware configuration for most modern Marlin.
    The diff_ir is only different in that the z endstop is no longer
    inverting.
    [Configuration.h, Configuration_adv.h]
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2018-07-16 Fixed the extruder_mount.stl
    It had been overridden by the Bowden version.
    [bowden_extruder_mount.stl, extruder_mount.scad, extruder_mount.stl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]
2018-07-16 Updated extruder and full with the correct mount
    [extruder_plate.stl, full_plate.stl]
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

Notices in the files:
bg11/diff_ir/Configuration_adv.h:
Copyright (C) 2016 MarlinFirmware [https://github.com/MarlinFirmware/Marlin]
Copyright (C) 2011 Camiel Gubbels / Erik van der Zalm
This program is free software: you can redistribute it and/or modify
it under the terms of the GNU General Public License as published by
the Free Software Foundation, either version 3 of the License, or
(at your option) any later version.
